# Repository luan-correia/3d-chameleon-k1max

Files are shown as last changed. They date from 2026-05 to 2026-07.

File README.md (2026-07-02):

# 3D Camaleao - 3D Chameleon modificado

Projeto de controle para um sistema tipo 3D Chameleon com:

- Raspberry Pi Pico controlando motores, sensores e comunicacao com a K1/Klipper
- ESP32 com display ST7789 atualizado, encoder e menu de configuracao
- 2 drivers TMC2209 em modo standalone
- sensores de filamento no hub, hotend, buffer e entradas T0 a T3
- arquivos Klipper e modelos STL do conjunto mecanico

Este repositorio esta organizado para documentar o hardware, os firmwares e os arquivos auxiliares usados no projeto.

## Instalacao automatica no Klipper

O instalador configura o daemon serial, as macros e o painel dedicado **Camaleao** no Mainsail. Ele detecta automaticamente Creality K1/Buildroot e instalacoes Linux comuns do Klipper.

```bash
git clone https://github.com/luan-correia/3d-chameleon-k1max.git
cd 3d-chameleon-k1max
sudo ./installer/install.sh
```

Depois da instalacao, reinicie o Klipper e atualize o navegador com `Ctrl+F5`. O instalador sempre cria backup antes de alterar arquivos.

Comandos de manutencao:

```bash
sudo ./installer/update.sh
sudo ./installer/diagnose.sh
sudo ./installer/uninstall.sh
```

Consulte [docs/instalador.md](docs/instalador.md) para requisitos, variaveis e recuperacao.

## Atualizacao do display

A versao atual substitui o display simples antigo por um painel com **ESP32 + ST7789 320x240**.

Antes, o controle visual ficava mais limitado. Agora o ESP32 faz a interface completa e conversa com o Pico por I2C. O Pico continua sendo responsavel pela logica principal dos motores e sensores.

O painel novo no ESP32 inclui:

- tela inicial com status das ferramentas T0 a T3
- status de hotend, buffer, impressao e comunicacao com o Pico
- menu por encoder
- load, unload, home, start e stop pelo display
- menu de configuracao
- calibracao e reset da calibracao
- ajuste de velocidade em porcentagem
- secador de filamento opcional, com controle de temperatura e umidade
- alertas visuais de filamento no hotend, filamento quebrado ou sensor com defeito
- logo `3DC CAMALEAO - VERSAO BRASIL`

Com essa mudanca, o projeto fica dividido assim:

```text
Pico  -> motores, sensores, comandos da K1/Klipper e seguranca
ESP32 -> display ST7789, encoder, menus, alertas e configuracao visual
```

## Estrutura

```text
firmware/
  esp32_display/
    platformio.ini
    src/ESP32_3D_Chameleon_ST7789_I2C_V16_GOTA_UMIDADE.ino
  pico/
    Pico_3D_Chameleon_I2C_COMPLETO.ino

docs/
  pinout.md
  funcionamento.md
  configuracao.md

camaleao e base/
  arquivos STL da base, hub e suporte

rebobinador/
  arquivos STL do rebobinador

klipper upgrade comunicao python e macros para camaleoa/
  macros Klipper e daemon Python

installer/
  instalacao, atualizacao, diagnostico e desinstalacao
```

## Estado atual do firmware

### Pico

O Pico e o controlador principal do sistema. Ele cuida de:

- motor seletor
- motor alimentador/extrusor
- sensores T0, T1, T2 e T3
- sensor unico do hub/saida
- sensor hotend
- sensores de buffer vazio e cheio
- endstop do seletor
- comandos USB serial vindos da K1/Klipper
- comunicacao I2C com o ESP32

### ESP32

O ESP32 cuida da interface:

- display ST7789 320x240
- encoder
- menu principal
- menu de configuracao
- alertas visuais
- envio de comandos para o Pico por I2C

O ESP32 nao movimenta os motores diretamente. Ele envia comandos para o Pico, e o Pico executa a acao com os sensores de seguranca.

## Aquecedor/secador opcional

O aquecedor e um recurso **opcional**. O 3D Camaleao funciona normalmente sem montar o secador; ele nao e necessario para selecionar, carregar ou descarregar filamento.

Quem quiser usar o recurso pode ligar ao ESP32:

| Funcao | Pino do ESP32 |
|---|---|
| Sensor de temperatura NTC | GPIO34 |
| Controle do aquecedor | GPIO26 |
| Controle do ventilador | GPIO14 |

O menu `SECAGEM FILAMENTO` permite definir temperatura e umidade. O firmware so aciona o aquecedor quando o NTC e identificado corretamente, desliga o aquecimento ao atingir o limite configurado e mantem o ventilador ligado durante o resfriamento ate a temperatura ficar abaixo de 30 C.

> **Atencao:** nao ligue o aquecedor diretamente ao ESP32. Use um modulo MOSFET adequado a tensao e corrente do aquecedor, fonte dimensionada, fusivel e protecao termica. Todos os GND devem estar em comum.

## Logica principal

- `LOAD`: carrega ate o sensor do hotend detectar filamento, depois anda mais 4 mm e enche o buffer.
- `UNLOAD`: descarrega ate o sensor do hub/saida indicar que o filamento saiu, usando a distancia configurada como limite de seguranca.
- A distancia de load/unload serve como protecao: se o filamento travar e o sensor nao mudar, o Pico para e informa erro.
- O buffer e mantido pela logica de reabastecimento durante impressao.
- O pre-load aciona quando um filamento entra no sensor de entrada, vai ate o sensor do hub e retrai 40 mm.

## Microsteps e distancia

O firmware atual assume:

```cpp
MICROSTEPS = 16
STEPS_PER_REV = 200
STEPS_PER_MM = 428.0
```

Os drivers TMC2209 estao em modo standalone. Por isso, o microstep real depende dos DIP switches/jumpers da placa do driver.

No teste atual:

- seletor funcionou com `1 2 3 ON`
- extrusor funcionou melhor com `1 ON`, `2 OFF`, `3 ON`

Se mudar a configuracao de microstep, pode ser necessario recalibrar ou ajustar `STEPS_PER_MM`.

## Como compilar o ESP32

O firmware do ESP32 usa PlatformIO.

```powershell
cd firmware\esp32_display
pio run
pio run -t upload
```

No projeto original, o upload estava usando `COM3`.

O arquivo principal do display atualizado fica em:

```text
firmware/esp32_display/src/ESP32_3D_Chameleon_ST7789_I2C_V16_GOTA_UMIDADE.ino
```

## Como gravar o Pico

Abra o arquivo do Pico na Arduino IDE ou ambiente equivalente com suporte ao Raspberry Pi Pico:

```text
firmware/pico/Pico_3D_Chameleon_I2C_COMPLETO.ino
```

Grave no Raspberry Pi Pico conectado por USB.

## Lista de materiais

| Quantidade | Item |
|---|---|
| 9 | Micro switch KW10-B |
| 1 | Raspberry Pi Pico |
| 1 | ESP32 |
| 1 | Encoder |
| 1 | Fonte 12 V ou 24 V 5 A |
| 1 | Step-down para 5 V 3 A |
| 2 | Suporte para driver |
| 2 | Driver TMC2209 ou A4988 |
| 1 | Display ST7789 240x320 |
| 4 | Parafuso M3 cabeca chata 10 mm |
| 8 | Parafuso M3 cabeca chata 15 mm com porcas |
| 4 | Parafuso M3 cabeca cilindrica 35 mm |
| 20 | Parafuso M3 cabeca cilindrica 6 mm |
| 8 | Parafuso M3 cabeca cilindrica 12 mm |
| 4 | Conector PTFE |
| 6 | Esfera de 4 mm |
| 2 m | Tubo PTFE 4 mm x 2.5 mm |
| 1 | Caixa acrilica 39 x 29 x 25 cm |
| 1 | Tomada interruptor AS-03 tripolar macho com chave gangorra |
| 1 | Porta USB tipo C |
| 4 | Molas: 8 mm de comprimento, 4 mm externo, arame de 1 mm ou 0.7 mm |
| 50 | Bucha de inserto metalico M3 x 4 mm |

Para o secador opcional, acrescente um sensor NTC, um aquecedor, um ventilador e um modulo MOSFET compativel com a carga utilizada.

## Observacoes importantes

- Todos os GND precisam estar em comum: Pico, ESP32, drivers e fonte dos motores.
- Os sinais do Pico sao 3.3 V.
- Nao conecte ou desconecte motor com o driver energizado.
- Ajuste a corrente dos TMC2209 antes de testar com filamento.
- Se o motor so vibrar, confira pares das bobinas, corrente do driver e DIP switches.

## Creditos e agradecimentos

Este projeto e uma adaptacao/modificacao feita para uso na Creality K1 Max, baseada na ideia do 3D Chameleon.

Agradecimentos aos projetos e comunidades que ajudaram como referencia:

- 3D Chameleon original: https://www.3dchameleon.com/
- Filamentalist Rewinder / ERCF: https://github.com/SkiBikePrint/Filamentalist
- ERCF v2: https://github.com/Carrot-collective/ERCF_v2

## Apoie o projeto

Se este projeto te ajudou e voce quiser apoiar para ele crescer, qualquer contribuicao ajuda nos testes, pecas, placas e melhorias.

PIX:

```text
47996781505
```

PayPal:

```text
luan.lec94@gmail.com
```

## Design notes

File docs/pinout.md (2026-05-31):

# Pinout

## Pico

### Sensores de entrada

```text
T0 entrada : GPIO 0
T1 entrada : GPIO 1
T2 entrada : GPIO 2
T3 entrada : GPIO 3
```

### I2C para ESP32

```text
SDA : GPIO 4
SCL : GPIO 5
Endereco I2C: 0x12
```

### Sensores principais

```text
Endstop seletor : GPIO 8
Sensor hotend   : GPIO 9
Buffer vazio    : GPIO 10
Buffer cheio    : GPIO 11
Sensor hub      : GPIO 12
```

### Motor seletor

```text
STEP : GPIO 16
DIR  : GPIO 17
EN   : GPIO 18
```

### Motor alimentador/extrusor

```text
STEP : GPIO 19
DIR  : GPIO 20
EN   : GPIO 21
```

## ESP32

### Display ST7789

```text
TFT_CS   : GPIO 15
TFT_DC   : GPIO 2
TFT_RST  : GPIO 4
TFT_MOSI : GPIO 23
TFT_SCLK : GPIO 18
```

### I2C para Pico

```text
SDA : GPIO 21
SCL : GPIO 22
```

### Encoder

```text
CLK : GPIO 32
DT  : GPIO 33
SW  : GPIO 25
```

### DHT22

```text
DATA : GPIO 27
```

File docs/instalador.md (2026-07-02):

# Instalador do painel Camaleao

O instalador adiciona uma placa exclusiva do 3D Camaleao ao dashboard do Mainsail e instala a comunicacao Python com o Pico.

## Sistemas suportados

- Creality K1, K1 Max e variantes com root, Moonraker e Mainsail
- Raspberry Pi e outros computadores Linux com Klipper, Moonraker, Mainsail, nginx e systemd

## Requisitos

- Pico gravado com o firmware deste repositorio
- Pico conectado por USB ao computador que executa o Klipper
- Python 3
- `unzip`
- acesso root ou `sudo`
- `gcode_shell_command.py` para usar as macros Klipper

O painel Mainsail funciona diretamente com o daemon. Caso `gcode_shell_command.py` nao esteja instalado, o diagnostico avisa e o painel ainda pode ser usado manualmente.

## Instalacao

```bash
git clone https://github.com/luan-correia/3d-chameleon-k1max.git
cd 3d-chameleon-k1max
sudo ./installer/install.sh
```

O processo:

1. Detecta K1/Buildroot ou Linux comum.
2. Localiza Mainsail, nginx e `printer.cfg`.
3. Detecta a porta do Pico.
4. Cria backup com data e hora.
5. Instala daemon, cliente e macros.
6. Instala o Mainsail personalizado em uma pasta separada.
7. Valida o nginx antes de ativar a configuracao.
8. Testa `/health` e o comando `STATUS` do Pico.

## Caminhos na K1

- Configuracao: `/usr/data/printer_data/config`
- Daemon: `/usr/data/printer_data/config/chameleon`
- Painel: `/usr/data/mainsail-chameleon`
- Estado: `/usr/data/chameleon_installer/state.env`
- Backups: `/usr/data/chameleon_backups/`

## Caminhos no Linux comum

- Daemon: `/opt/chameleon`
- Painel: `/opt/mainsail-chameleon`
- Servico: `chameleon-daemon.service`
- Estado: `/var/lib/chameleon-installer/state.env`
- Backups: `/var/backups/chameleon/`

## Configuracao manual de caminhos

Se a deteccao automatica nao encontrar algum componente, informe antes do comando:

```bash
sudo CHAMELEON_SERIAL_PORT=/dev/ttyACM0 \
  CHAMELEON_CONFIG_DIR=/home/pi/printer_data/config \
  CHAMELEON_MAINSAIL_DIR=/home/pi/mainsail \
  CHAMELEON_NGINX_CONF=/etc/nginx/sites-enabled/mainsail \
  ./installer/install.sh
```

## Diagnostico

```bash
sudo ./installer/diagnose.sh
```

Ele mostra porta serial, respostas do daemon, `STATUS` do Pico, processos e caminhos instalados.

## Atualizacao

```bash
sudo ./installer/update.sh
```

O atualizador busca o repositorio e executa novamente a instalacao, criando outro backup.

## Desinstalacao

```bash
sudo ./installer/uninstall.sh
```

O desinstalador restaura o nginx salvo, remove painel, daemon e include das macros. Os backups permanecem guardados.

## Codigo-fonte do painel

O painel foi criado sobre o Mainsail `v2.17.0`. O patch utilizado para gerar o pacote esta em `installer/mainsail-src/mainsail-v2.17.0-chameleon.patch`.

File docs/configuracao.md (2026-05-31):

# Configuracao

## Menu do ESP32

O menu do ESP32 permite:

- selecionar ferramentas T0 a T3
- executar load e unload
- fazer home
- iniciar/parar impressao
- calibrar distancia
- ajustar velocidade
- ajustar rampa
- resetar configuracao de calibracao

## Velocidades

O display mostra velocidades em porcentagem.

```text
100% = 70 mm/s
```

As velocidades principais sao:

- `VEL LOAD/UN`: velocidade rapida de load/unload
- `VEL RAMPA`: velocidade da parte final da rampa
- `RAMPA MM`: quantidade de milimetros antes do fim onde a rampa comeca

## Calibracao

A calibracao mede a distancia ate o sensor do hotend. O valor salvo e usado como base para o limite de seguranca dos movimentos.

Exemplo:

```text
calibracao = 560 mm
distancia configurada = 700 mm
```

Nesse caso, o `LOAD` continua parando no sensor do hotend. Os 700 mm sao apenas limite para detectar erro se o filamento travar.

## Reset de calibracao

O menu possui uma opcao para resetar a configuracao de calibracao. Isso invalida a configuracao salva e volta aos valores padrao.

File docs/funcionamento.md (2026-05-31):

# Funcionamento

## LOAD

O comando `LOAD` faz:

1. Verifica se o filamento ja esta no hotend.
2. Se nao estiver, gira o motor alimentador no sentido de load.
3. Para quando o sensor do hotend detectar filamento.
4. Anda mais 4 mm para encostar o filamento.
5. Enche o buffer.

A distancia configurada e usada como limite de seguranca. Se o sensor do hotend nao acionar dentro do limite, o Pico para e informa erro.

## UNLOAD

O comando `UNLOAD` faz:

1. Desativa o modo buffer drain, se estiver ativo.
2. Gira o motor alimentador no sentido de unload.
3. Para quando o sensor do hub/saida indicar que o filamento saiu.
4. Retrai mais 40 mm para o filamento nao sair do Camaleao.

A distancia configurada tambem e limite de seguranca. Se o sensor nao mudar, o Pico para e informa erro.

## PRE-LOAD

O pre-load e acionado quando um sensor de entrada muda de sem filamento para com filamento.

Fluxo:

1. Confere se o hub esta livre.
2. Se o hub ja tiver filamento, ignora para evitar colisao.
3. Move o seletor para a ferramenta detectada.
4. Empurra ate o sensor do hub detectar filamento.
5. Retrai 40 mm.

## Buffer

Durante a impressao, o Pico monitora os sensores de buffer. Quando o buffer fica vazio e o hotend ainda tem filamento, ele reabastece ate o sensor de buffer cheio.

## Alertas no ESP32

O display mostra alertas quando:

- o hotend detecta filamento e o hub nao detecta, indicando possivel filamento quebrado ou sensor com defeito
- hub e hotend detectam filamento, indicando que o filamento ja esta no hotend

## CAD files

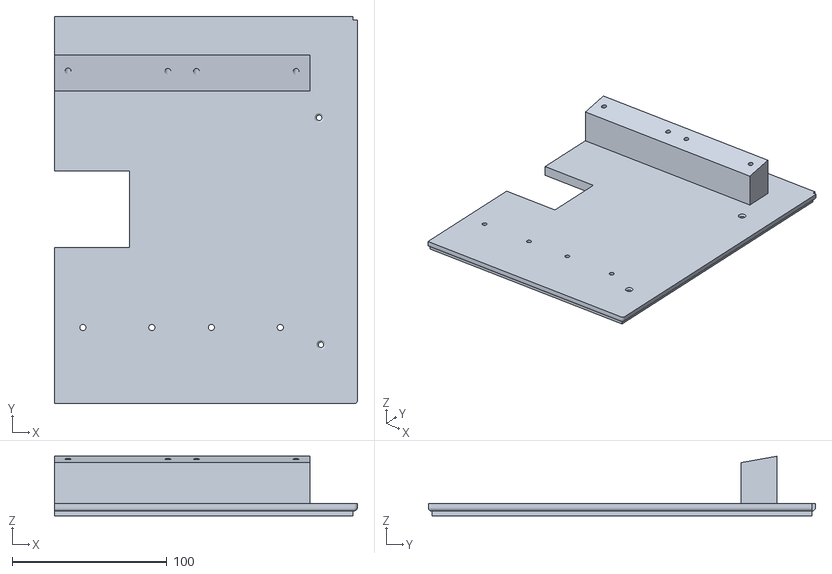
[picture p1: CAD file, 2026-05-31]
camaleao e base/tampa base 2 tampa base para nema 17 42.stl
195.7 x 250.2 x 38.4

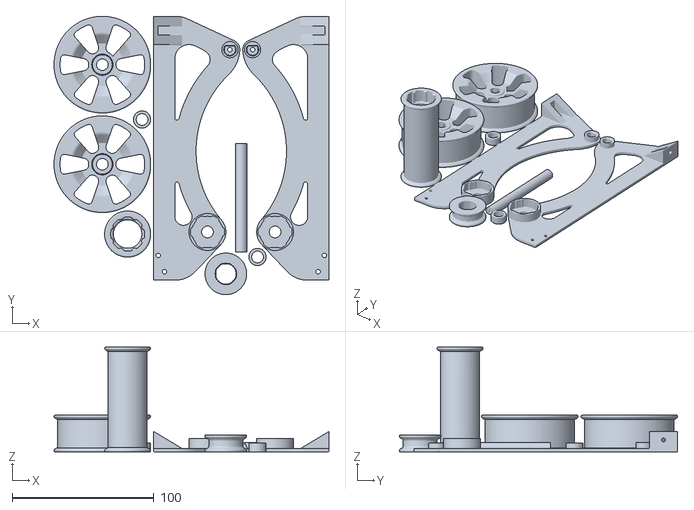
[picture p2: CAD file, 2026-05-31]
rebobinador/filamentalist.stl
193.8 x 196.2 x 74.0

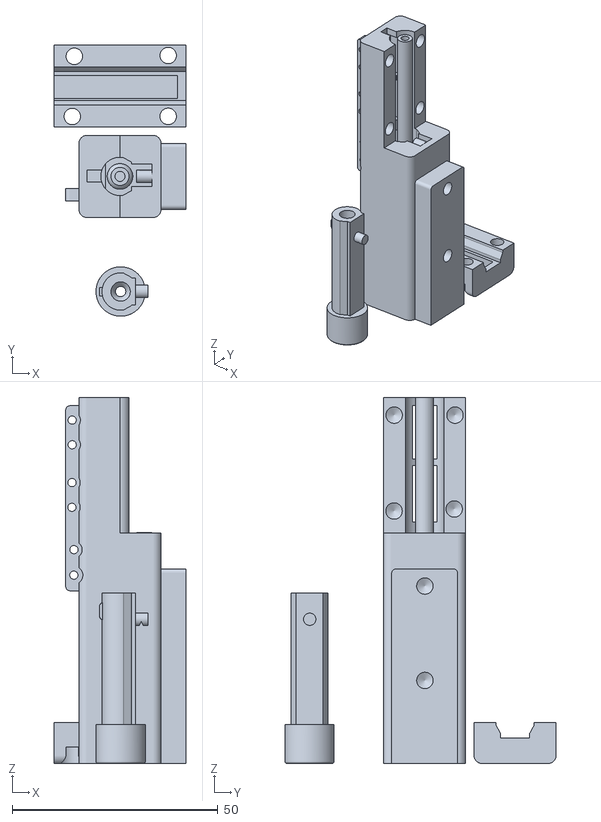
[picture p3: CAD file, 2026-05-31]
camaleao e base/hub buffe v2.stl
32.0 x 66.0 x 89.0

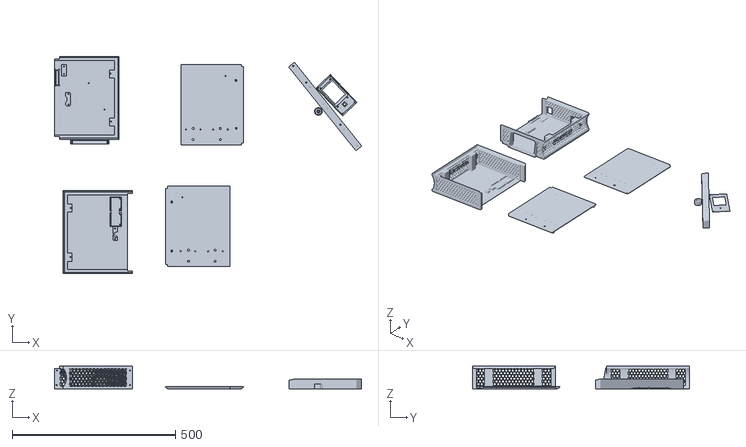
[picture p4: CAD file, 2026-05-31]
camaleao e base/base para camaleao com display.stl
939.0 x 665.1 x 70.0

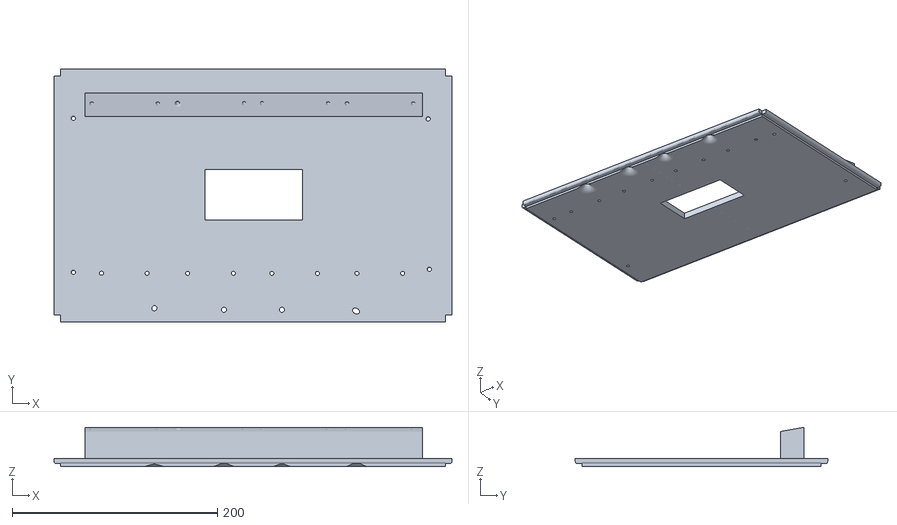
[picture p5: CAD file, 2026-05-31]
camaleao e base/tampa base para nema 17 42.stl
388.0 x 246.2 x 38.4

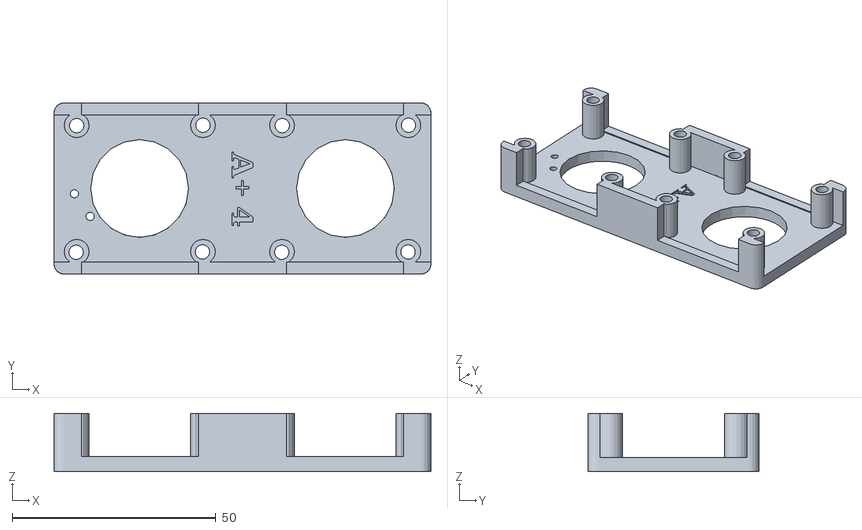
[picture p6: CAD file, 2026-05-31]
camaleao e base/camaelao 4.0 A+ com sensor home.stl
92.5 x 42.0 x 14.2

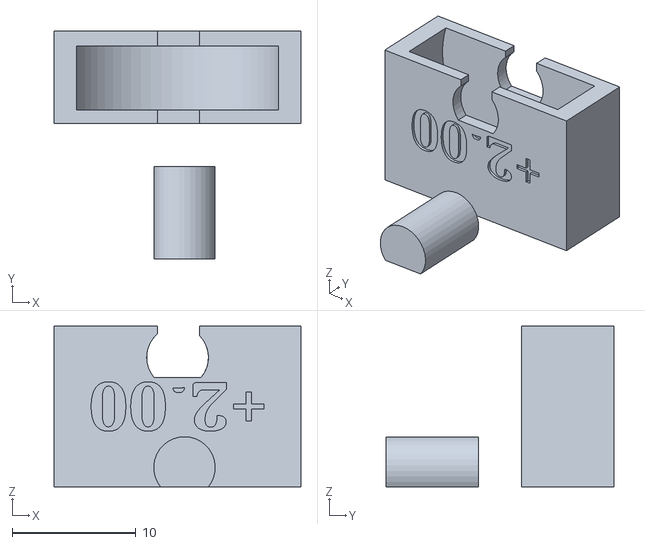
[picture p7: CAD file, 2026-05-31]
camaleao e base/suporte do rolamento de tensao do filamento.stl
20.0 x 18.5 x 13.0

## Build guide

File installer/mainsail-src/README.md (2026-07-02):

# Fonte do painel Mainsail

O arquivo `mainsail-v2.17.0-chameleon.patch` contem as mudancas aplicadas ao Mainsail oficial `v2.17.0`.

Para recompilar:

```bash
git clone --branch v2.17.0 https://github.com/mainsail-crew/mainsail.git
cd mainsail
git apply ../mainsail-v2.17.0-chameleon.patch
npm install
npm run build
```

O conteudo gerado em `dist/` deve ser compactado na raiz do ZIP e colocado em `installer/assets/mainsail-chameleon.zip`.

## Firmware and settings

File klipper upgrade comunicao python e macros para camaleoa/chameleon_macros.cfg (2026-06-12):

########################################################################################################################
# chameleon_macros.cfg — 3D Chameleon K1 Max
# Comunicação via USB Serial → Pico usando gcode_shell_command
#
# Setup:
#   1. Pico conectado via USB na K1
#   2. chameleon_bridge.py em /usr/data/chameleon_bridge.py
#   3. pip3 install pyserial
#   4. gcode_shell_command.py em /usr/share/klipper/klippy/extras/
#   5. Verificar porta: ls /dev/ttyACM* /dev/ttyUSB*
#   6. Ajustar ARDUINO_PORT no chameleon_bridge.py se necessário
#
# No printer.cfg adicionar:
#   [include chameleon_macros.cfg]
#
# Switch do hotend conectado direto no Pico GPIO9
# Não precisa de filament_switch_sensor no printer.cfg
#
# Start Gcode Creality Print:
#   CHAMELEON_PRINT_START TOOL=[initial_no_support_extruder]
#
# End Gcode:
#   CHAMELEON_PRINT_END
########################################################################################################################


# ══════════════════════════════════════════════════════════════════════════════
# SHELL COMMAND
# ══════════════════════════════════════════════════════════════════════════════

[gcode_shell_command chameleon_cmd]
command: python3 /usr/data/printer_data/config/chameleon/chameleon_client.py
timeout: 120
verbose: True

[gcode_shell_command chameleon_daemon_start]
command: /bin/sh /usr/data/printer_data/config/chameleon/chameleon-daemon.init start
timeout: 10
verbose: False

[delayed_gcode CHAMELEON_DAEMON_AUTOSTART]
initial_duration: 15
gcode:
    RUN_SHELL_COMMAND CMD=chameleon_daemon_start


# ══════════════════════════════════════════════════════════════════════════════
# VARIÁVEIS GLOBAIS
# ══════════════════════════════════════════════════════════════════════════════

[gcode_macro _CHAMELEON_VARS]
variable_tool: 0
variable_enabled: 1
variable_runout_paused: 0
variable_waiting_initial_tool: 0
gcode:
    # macro de variáveis — não executa nada


# ══════════════════════════════════════════════════════════════════════════════
# FIL_CUT — ativa buffer drain, Z hop, retrai, corta e vai para posição de purga
#
# Fluxo:
#   1. BUFFER_DRAIN → Pico esvazia buffer se cheio, ativa modo drain em background
#                     responde imediatamente, macro continua
#   2. Z hop +5mm relativo à peça atual
#   3. Move para cortador, retrai 40mm + corte duplo + retrai 70mm
#      (retração enche buffer → Pico esvazia automaticamente)
#   4. Move para posição de purga X304 Y250 Z0.2 e aguarda
#      RESTORE feito somente após Purga
# ══════════════════════════════════════════════════════════════════════════════

[gcode_macro CHAMELEON_ENABLE]
description: Ativa o MMU 3D Chameleon
gcode:
    SET_GCODE_VARIABLE MACRO=_CHAMELEON_VARS VARIABLE=enabled VALUE=1
    RESPOND MSG="Chameleon: MMU ativado."


[gcode_macro CHAMELEON_DISABLE]
description: Desativa o MMU para imprimir com filamento externo
gcode:
    SET_GCODE_VARIABLE MACRO=_CHAMELEON_VARS VARIABLE=enabled VALUE=0
    RESPOND MSG="Chameleon: MMU desativado. Comandos de troca serao ignorados."


[gcode_macro Fil_Cut]
description: Ativa buffer drain, Z hop, retrai, corta e vai para posição de purga
gcode:
    SAVE_GCODE_STATE NAME=troca_state
    {% set z_hop = 5.0 %}
    {% set max_z = printer.toolhead.axis_maximum.z %}
    {% set cur_z = printer.toolhead.position.z %}
    {% set safe_z = [cur_z + z_hop, max_z] | min %}

    # 1. Pico entra em modo BUFFER_DRAIN — responde imediatamente
    RESPOND MSG="🐍 Fil_Cut: ativando buffer drain..."
    RUN_SHELL_COMMAND CMD=chameleon_cmd PARAMS="BUFFER_DRAIN"

    # 2. Z hop seguro antes de mover
    G90
    G0 Z{safe_z} F3000

    # 3. Move para cortador
    RESPOND MSG="🐍 Fil_Cut: movendo para cortador..."
    G90
    M83

    G0 X34 Y280 F15000
    G1 E-38 F800              # Retrai 40mm rapido

    G0 X24 Y280 F15000
    G0 Y305 F1000

    # 4. Corte duplo
    RESPOND MSG="🐍 Fil_Cut: cortando..."
    G0 X7 F2000
    G0 X24 F10000
    G0 X7 F2000
    G0 X24 Y280 F10000

    G1 E-50 F1500              # Retrai 50mm rapido apos corte

    # 5. Move para posição de purga e aguarda novo filamento
    RESPOND MSG="Fil_Cut: corte concluido, chamando unload..."


# ══════════════════════════════════════════════════════════════════════════════
# PURGA — bico já está na posição X304 Y250 Z0.2 vindo do Fil_Cut
# ══════════════════════════════════════════════════════════════════════════════

[gcode_macro FIL_CUT_END]
description: Corte final - retrai, corta e faz unload sem ir para purga
gcode:
    {% set vars = printer["gcode_macro _CHAMELEON_VARS"] %}
    {% set enabled = vars.enabled|int %}
    {% set current_tool = vars.tool|int %}

    {% if not enabled %}
        RESPOND MSG="Chameleon: MMU desativado, FIL_CUT_END ignorado."
    {% else %}
        {% set z_hop = 5.0 %}
        {% set max_z = printer.toolhead.axis_maximum.z %}
        {% set cur_z = printer.toolhead.position.z %}
        {% set safe_z = [cur_z + z_hop, max_z] | min %}

        RESPOND MSG="Chameleon End: buffer drain..."
        RUN_SHELL_COMMAND CMD=chameleon_cmd PARAMS="BUFFER_DRAIN"

        G90
        G0 Z{safe_z} F3000

        RESPOND MSG="Chameleon End: movendo para cortador..."
        M83
        G0 X34 Y280 F15000
        G1 E-30 F800
        G0 X24 Y280 F15000
        G0 Y305 F1000

        RESPOND MSG="Chameleon End: cortando..."
        G0 X5 F2000
        G0 X24 F10000
        G0 X5 F2000
        G0 X24 Y280 F10000
        G4 P1500
        G1 E-50 F1500
        
        M400 
        
        G4 P500  
        
   

        RESPOND MSG="Chameleon End: descarregando T{current_tool}..."
        RUN_SHELL_COMMAND CMD=chameleon_cmd PARAMS="T{current_tool}"
        RUN_SHELL_COMMAND CMD=chameleon_cmd PARAMS="UNLOAD"
    {% endif %}

[gcode_macro Purga]
gcode:
    {% set current_temp = printer.extruder.target %}
    G90
    M83

    RESPOND MSG="Purga: formando torre na borda..."
    G0 X300 Y250 F15000
    G0 Z0.20 F2000


    G1 E70 F350
    G0 Z2 F1000 
    
    M106 S255
    
    G1 E10 F250
    G0 Z3 F1000
    G1 E10 F250
    G0 Z4 F1000
    G1 E10 F250
    G0 Z5 F1000
    G1 E10 F250
    G0 Z6 F1000
    G1 E-1 F300

    G4 P3000

    RESPOND MSG="Purga: empurrando descarte para fora da mesa..."
    G0 Z15  F1000
    G0 X280  F16000
    G0 Z2 F1000
    G0 X304 F6000
  

    G0 Z3 F3000
    M106 S0

    RESPOND MSG="Purga: limpando bico no silicone..."
    G0 X301 Y280 F15000
    G0 Y250 F15000
    G0 Y290 F15000
    G0 Y250 F15000
    G0 Y290 F15000
    G0 Y250 F15000

    RESPOND MSG="Purga: concluida."
    M104 S{current_temp}
    RESTORE_GCODE_STATE NAME=troca_state MOVE=0


[gcode_macro Purga_Inicial]
gcode:
    {% set current_temp = printer.extruder.target %}
    G90
    M83

    RESPOND MSG="Purga inicial: formando torre maior na borda..."
    G0 X300 Y250 F15000
    G0 Z0.20 F2000


    G1 E70 F350
    G0 Z2 F1000

    M106 S255

    G1 E20 F250
    G0 Z3 F1000
    G1 E20 F250
    G0 Z4 F1000
    G1 E20 F250
    G0 Z5 F1000
    G1 E10 F300
    G0 Z6 F1000
    G1 E10 F250
    G0 Z7 F1000
    G1 E10 F1000
    G0 Z9 F1000
    G1 E10 F1000
    G0 Z8 F1000
    G1 E10 F1000
    G0 Z10 F1000
    G1 E-0.2 F300

    G4 P3000

    RESPOND MSG="Purga inicial: empurrando descarte para fora da mesa..."
    G0 Z15  F1000
    G0 X280  F16000
    G0 Z2 F1000
    G0 X304 F6000


    G0 Z3 F3000
    M106 S0

    RESPOND MSG="Purga inicial: limpando bico no silicone..."
    G0 X301 Y280 F15000
    G0 Y250 F15000
    G0 Y290 F15000
    G0 Y250 F15000
    G0 Y290 F15000
    G0 Y250 F15000

    RESPOND MSG="Purga inicial: concluida."
    M104 S{current_temp}
    RESTORE_GCODE_STATE NAME=troca_state MOVE=0




# ══════════════════════════════════════════════════════════════════════════════
# LOAD_ATE_SENSOR — Pico empurra até GPIO9 acionar
# Se filamento já presente retorna imediatamente
# Após Load OK o buffer ativa automaticamente no Pico
# ══════════════════════════════════════════════════════════════════════════════

[gcode_macro Load_Ate_Sensor]
description: LOAD contínuo — para quando sensor hotend GPIO9 acionar
gcode:
    RESPOND MSG="🐍 Load: empurrando até sensor..."
    RUN_SHELL_COMMAND CMD=chameleon_cmd PARAMS="LOAD"
    RESPOND MSG="🐍 Load: filamento chegou ao sensor!"


# ══════════════════════════════════════════════════════════════════════════════
# SEQUÊNCIA DE TROCA COMPLETA
#
# Fluxo:
#   1. Fil_Cut         → BUFFER_DRAIN + Z hop + retrai + corta + vai para purga
#   2. T{atual}+UNLOAD → Pico sai do drain + descarrega até sensor saída
#   3. T{novo}         → seletor move para novo gate
#   4. Load_Ate_Sensor → Pico empurra até GPIO9 acionar → buffer ativa
#   5. Purga           → purga + limpa + volta para peça
# ══════════════════════════════════════════════════════════════════════════════
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

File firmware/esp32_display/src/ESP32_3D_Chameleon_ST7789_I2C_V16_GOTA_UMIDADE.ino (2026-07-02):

/* ════════════════════════════════════════════════════════════════════════
   3D CHAMELEON MK4
   ESP32 + ST7789 320x240
   LAYOUT CLEAN V14 — I2C Pico + ATIVO por LOAD + Menos Pisca
════════════════════════════════════════════════════════════════════════ */

#include <Adafruit_GFX.h>
#include <Adafruit_ST7789.h>
#include <SPI.h>
#include <Wire.h>
#include <DHT.h>
#include <Preferences.h>

// ═══════════════════════════════════════
// DISPLAY (VSPI — pinos padrao)
// ═══════════════════════════════════════

#define TFT_CS    15
#define TFT_DC     2
#define TFT_RST    4
#define TFT_MOSI  23
#define TFT_SCLK  18

Adafruit_ST7789 tft = Adafruit_ST7789(TFT_CS, TFT_DC, TFT_RST);

// ═══════════════════════════════════════
// I2C PICO (ESP32 mestre / Pico escravo)
//
// Ligacao ESP32 <-> Pico:
//   ESP GPIO21 (SDA) -> Pico GPIO4 (SDA)
//   ESP GPIO22 (SCL) -> Pico GPIO5 (SCL)
//   GND              -> GND
//
// Use pull-up de 4.7k em SDA e SCL para 3.3V.
// ═══════════════════════════════════════

#define PICO_I2C_SDA   21
#define PICO_I2C_SCL   22
#define PICO_I2C_ADDR  0x12

#define I2C_CMD_SIZE   4
#define I2C_STA_SIZE   16
#define I2C_SOF_CMD    0xAA
#define I2C_SOF_STA    0xBB
#define STEPS_PER_MM_F 428.0f
#define CONFIG_SPEED_MAX_MMS_F 70.0f

// Comandos
#define CMD_T0          0x01
#define CMD_T1          0x02
#define CMD_T2          0x03
#define CMD_T3          0x04
#define CMD_LOAD        0x05
#define CMD_UNLOAD      0x06
#define CMD_HOME        0x07
#define CMD_START_PRINT 0x08
#define CMD_STOP_PRINT  0x09
#define CMD_STATUS      0x0A
#define CMD_CALIBRAR    0x70
#define CMD_SPD_FAST_UP  0x80
#define CMD_SPD_FAST_DN  0x81
#define CMD_SPD_RAMP_UP  0x82
#define CMD_SPD_RAMP_DN  0x83
#define CMD_RAMP_MM_UP   0x84
#define CMD_RAMP_MM_DN   0x85
#define CMD_DIST_UP      0x86
#define CMD_DIST_DN      0x87
#define CMD_RESET_CONFIG 0x88

// Status do Pico
#define STA_IDLE     0x00
#define STA_BUSY     0x01
#define STA_PRINTING 0x02
#define STA_ERROR    0x03

// ═══════════════════════════════════════
// DHT22
// ═══════════════════════════════════════

#define DHT_PIN  27
#define DHT_TYPE DHT22
DHT dht(DHT_PIN, DHT_TYPE);

// Secagem de filamento (controle local no ESP32)
#define NTC_PIN       34
#define HEATER_PIN    26
#define DRYER_FAN_PIN 14

const float NTC_FIXED_OHMS = 100000.0f;
const float NTC_NOMINAL_OHMS = 100000.0f;
const float NTC_NOMINAL_C = 25.0f;
const float NTC_BETA = 3950.0f;
const float DRYER_COOLDOWN_C = 30.0f;
const float DRYER_HYSTERESIS_C = 1.0f;

// ═══════════════════════════════════════
// PREFERENCES
// ═══════════════════════════════════════

Preferences prefs;

// ═══════════════════════════════════════
// ENCODER
// ═══════════════════════════════════════

#define ENC_CLK 32
#define ENC_DT  33
#define ENC_SW  25

volatile int      encDelta         = 0;
volatile bool     btnPressed       = false;
volatile uint32_t lastBtnInterrupt = 0;
const int         ENC_COUNTS_PER_STEP = 2;
int               lastCLK_val      = HIGH;

// ═══════════════════════════════════════
// CORES
// ═══════════════════════════════════════

#define C_BG     0x0841
#define C_WHITE  0xFFFF
#define C_BLACK  0x0000
#define C_GRAY   0x7BEF
#define C_DARK   0x2104
#define C_CYAN   0x07FF
#define C_RED    0xF800
#define C_BLUE   0x001F
#define C_ORANGE 0xFD20
#define C_YELLOW 0xFFE0
#define C_ACTIVE 0x05BF
#define C_GREEN  0x07E0

const int COLOR_COUNT = 11;
const char* colorNames[COLOR_COUNT] = {
  "VERMELHO","VERDE","AZUL","AMARELO","LARANJA",
  "ROXO","BRANCO","CINZA","ROSA","MARROM","PRETO"
};
const uint16_t colorValues[COLOR_COUNT] = {
  0xF800, 0x07E0, 0x001F, 0xFFE0, 0xFD20,
  0x780F, 0xFFFF, 0x7BEF, 0xF81F, 0x8200, 0x0000
};

uint16_t toolColors[4] = { 0xF800, 0x07E0, 0x001F, 0xFFE0 };

// ═══════════════════════════════════════
// ESTADO ATUAL E ANTERIOR
// ═══════════════════════════════════════

struct ChameleonState {
  int   toolAtiva    = 0;
  bool  filamento[4] = { false, false, false, false };
  bool  bufferCheio  = false;
  bool  hub          = false;
  bool  hotend       = false;
  bool  imprimindo   = false;
  bool  unloadError  = false;
  float temperatura  = 0;
  float umidade      = 0;
  bool  picoOK       = false;
};

ChameleonState state;
ChameleonState prevState;
uint8_t picoStatusCode = STA_IDLE;

// Controle local do ESP32: etiqueta ATIVO aparece somente depois de LOAD
// e some depois de UNLOAD. Nao depende apenas da tool selecionada.
bool toolLoaded[4]     = { false, false, false, false };
bool prevToolLoaded[4] = { false, false, false, false };

bool homeDrawn = false;
bool unloadErrorShown = false;
bool prevDryerActive = false;

// ═══════════════════════════════════════
// NAVEGACAO
// ═══════════════════════════════════════

enum Screen {
  SCR_HOME,
  SCR_MENU,
  SCR_TOOL_ACTION,
  SCR_COLOR_SELECT,
  SCR_CONFIG,        // submenu de configuracoes
  SCR_DRYER
};

struct DryerState {
  float temperature = NAN;
  int targetTemperature = 50;
  int targetHumidity = 20;
  bool ntcOK = false;
  bool active = false;
  bool cooling = false;
  bool heaterOn = false;
  bool fanOn = false;
};

DryerState dryer;
int dryerIdx = 0;
bool dryerEditing = false;
const int DRYER_COUNT = 4;
unsigned long lastDryerControl = 0;
unsigned long lastDryerDraw = 0;

// Estado das configuracoes recebidas do Pico
struct ConfigState {
  float distMax  = 4000.0;
  int   spdFast  = 28;
  int   spdRamp  = 1325;
  float rampMM   = 60.0;
  bool  calibrado = false;
};

ConfigState cfg;

// Qual item do submenu config esta sendo editado
int cfgIdx = 0;
bool cfgEditing = false;
int cfgFastPercentEdit = 0;
int cfgRampPercentEdit = 0;

const int CONFIG_COUNT = 7;  // Calibrar + 4 ajustes + Reset + Voltar

Screen currentScreen = SCR_HOME;

int menuIdx      = 0;
int prevMenuIdx  = -1;
int toolActionIdx = 0;
int selectedToolIdx = 0;
int colorToolIdx = 0;
int colorPickIdx = 0;

const int TOOL_ACTION_COUNT = 4;
const char* toolActionLabels[TOOL_ACTION_COUNT] = {
  "EXTRUSAO",
  "RETRAIR",
  "COR FILAMENTO",
  "< VOLTAR"
};

// ═══════════════════════════════════════
// MENU
// ═══════════════════════════════════════

const int   MENU_COUNT = 12;
const char* menuLabels[MENU_COUNT] = {
  "< VOLTAR",
  "FILAMENTO T0","FILAMENTO T1","FILAMENTO T2","FILAMENTO T3",
  "LOAD","UNLOAD","HOME",
  "START","STOP",
  "SECAGEM FILAMENTO",
  "CONFIGURACAO"
};
const uint8_t menuCmds[MENU_COUNT] = {
  0x00,
  CMD_T0, CMD_T1, CMD_T2, CMD_T3,
  CMD_LOAD, CMD_UNLOAD, CMD_HOME,
  CMD_START_PRINT, CMD_STOP_PRINT,
  0x00,
  0x00  // CONFIGURACAO — tratado localmente
};

// ═══════════════════════════════════════
// FEEDBACK
// ═══════════════════════════════════════

bool          showingFeedback = false;
unsigned long feedbackStart   = 0;

// ═══════════════════════════════════════
// TIMERS
// ═══════════════════════════════════════

unsigned long lastDHT     = 0;
unsigned long lastRefresh = 0;

// ═══════════════════════════════════════
// ISR
// ═══════════════════════════════════════

void IRAM_ATTR encoderISR() {
  int clk = digitalRead(ENC_CLK);
  int dt  = digitalRead(ENC_DT);
  if (clk != lastCLK_val) {
    encDelta += (dt != clk) ? 1 : -1;
    lastCLK_val = clk;
  }
}

void IRAM_ATTR buttonISR() {
  uint32_t now = millis();
  if (now - lastBtnInterrupt > 500) {
    btnPressed       = true;
    lastBtnInterrupt = now;
  }
}

// ═══════════════════════════════════════
// I2C PICO
// ═══════════════════════════════════════

uint8_t i2cChecksum(uint8_t* buf, int len) {
  uint8_t chk = 0;
  for (int i = 0; i < len; i++) chk ^= buf[i];
  return chk;
}

bool picoReadStatus() {
  uint8_t rxBuf[I2C_STA_SIZE] = {0};

  int n = Wire.requestFrom(PICO_I2C_ADDR, I2C_STA_SIZE);
  if (n != I2C_STA_SIZE) {
    while (Wire.available()) Wire.read();
    return false;
  }

  for (int i = 0; i < I2C_STA_SIZE; i++) {
    rxBuf[i] = Wire.read();
  }

  if (rxBuf[0] != I2C_SOF_STA) return false;
  if (i2cChecksum(rxBuf, I2C_STA_SIZE - 1) != rxBuf[I2C_STA_SIZE - 1]) return false;

  // Pico envia:
  // [0xBB][STA][T][FILS][BUF][HE][FLAGS][DIST_LH][FAST_LH][RAMP_LH][RAMP_MM_LH][CHK]
  uint8_t sta  = rxBuf[1];
  uint8_t tool = rxBuf[2];
  uint8_t fils = rxBuf[3];
  uint8_t flags = rxBuf[6];

  state.picoOK    = true;
  state.toolAtiva = (tool > 0 && tool <= 4) ? tool - 1 : 0;
  picoStatusCode  = sta;

  for (int i = 0; i < 4; i++) {
    state.filamento[i] = (fils >> i) & 0x01;
  }

  state.bufferCheio = rxBuf[4] & 0x01;
  state.hub         = rxBuf[4] & 0x02;
  state.hotend      = rxBuf[5] & 0x01;
  state.imprimindo  = (sta == STA_PRINTING) || (flags & 0x01);
  state.unloadError = flags & 0x04;

  cfg.calibrado = flags & 0x02;
  cfg.distMax   = (float)((uint16_t)rxBuf[7]  | ((uint16_t)rxBuf[8]  << 8));
  cfg.spdFast   =         (uint16_t)rxBuf[9]  | ((uint16_t)rxBuf[10] << 8);
  cfg.spdRamp   =         (uint16_t)rxBuf[11] | ((uint16_t)rxBuf[12] << 8);
  cfg.rampMM    = (float)((uint16_t)rxBuf[13] | ((uint16_t)rxBuf[14] << 8));

  return true;
}

bool picoSendOnly(uint8_t cmd, uint8_t arg = 0) {
  uint8_t txBuf[I2C_CMD_SIZE] = {0};

  txBuf[0] = I2C_SOF_CMD;
  txBuf[1] = cmd;
  txBuf[2] = arg;
  txBuf[3] = i2cChecksum(txBuf, 3);

  Wire.beginTransmission(PICO_I2C_ADDR);
  Wire.write(txBuf, I2C_CMD_SIZE);
  uint8_t err = Wire.endTransmission();

  return err == 0;
}

bool picoTransaction(uint8_t cmd, uint8_t arg = 0) {
  if (!picoSendOnly(cmd, arg)) return false;
  delay(10);
  return picoReadStatus();
}

void picoPollStatus() {
  // Primeiro tenta leitura direta; se falhar, tenta pedir STATUS.
  if (!picoReadStatus()) {
    if (!picoTransaction(CMD_STATUS)) {
      state.picoOK = false;
    }
  }
}

bool picoSendCommand(uint8_t cmd, uint8_t arg = 0) {
  bool ok = picoTransaction(cmd, arg);
  if (!ok) {
    delay(60);
    ok = picoTransaction(cmd, arg);
  }
  return ok;
}

bool picoSendCommandWait(uint8_t cmd, uint8_t arg = 0, unsigned long timeoutMs = 30000) {
  if (!picoSendOnly(cmd, arg)) return false;

  unsigned long start = millis();
  bool gotStatus = false;

  while (millis() - start < timeoutMs) {
    delay(120);
    if (picoReadStatus()) {
      gotStatus = true;
      if (picoStatusCode != STA_BUSY) return picoStatusCode != STA_ERROR;
    }
  }

  return gotStatus && picoStatusCode != STA_ERROR;
}

float speedUsToMMS(uint16_t delayUs) {
  if (delayUs == 0) return 0.0f;
  return 1000000.0f / (2.0f * (float)delayUs * STEPS_PER_MM_F);
}

void printSpeedPercent(uint16_t delayUs) {
  float mmS = speedUsToMMS(delayUs);
  int percent = (int)((mmS * 100.0f / CONFIG_SPEED_MAX_MMS_F) + 0.5f);
  if (percent < 1 && mmS > 0.0f) percent = 1;
  if (percent > 100) percent = 100;
  tft.print(percent);
  tft.print("%");
}

int speedUsToPercent(uint16_t delayUs) {
  float mmS = speedUsToMMS(delayUs);
  int percent = (int)((mmS * 100.0f / CONFIG_SPEED_MAX_MMS_F) + 0.5f);
  if (percent < 1 && mmS > 0.0f) percent = 1;
  if (percent > 100) percent = 100;
  return percent;
}

uint16_t percentToSpeedUs(int percent) {
  if (percent < 1) percent = 1;
  if (percent > 100) percent = 100;
  float mmS = CONFIG_SPEED_MAX_MMS_F * ((float)percent / 100.0f);
  float delayUs = 1000000.0f / (2.0f * mmS * STEPS_PER_MM_F);
  if (delayUs < 10.0f) delayUs = 10.0f;
  if (delayUs > 5000.0f) delayUs = 5000.0f;
  return (uint16_t)(delayUs + 0.5f);
}

void printSpeedValue(uint16_t delayUs) {
  float mmS = speedUsToMMS(delayUs);
  if (mmS >= 10.0f) tft.print((int)(mmS + 0.5f));
  else tft.print(mmS, 1);
  tft.print("mm/s");
}

// ═══════════════════════════════════════
// PREFERENCES
// ═══════════════════════════════════════

void saveColors() {
  prefs.begin("chameleon", false);
  prefs.putUShort("c0", toolColors[0]);
  prefs.putUShort("c1", toolColors[1]);
  prefs.putUShort("c2", toolColors[2]);
  prefs.putUShort("c3", toolColors[3]);
  prefs.end();
}

void loadColors() {
  prefs.begin("chameleon", true);
  toolColors[0] = prefs.getUShort("c0", 0xF800);
  toolColors[1] = prefs.getUShort("c1", 0x07E0);
  toolColors[2] = prefs.getUShort("c2", 0x001F);
  toolColors[3] = prefs.getUShort("c3", 0xFFE0);
  prefs.end();
}

// ═══════════════════════════════════════
// DHT
// ═══════════════════════════════════════

void readDHT() {
  float t = dht.readTemperature();
  float h = dht.readHumidity();
  if (!isnan(t)) state.temperatura = t;
  if (!isnan(h)) state.umidade     = h;
}

// ═══════════════════════════════════════
// COPIA ESTADO
// ═══════════════════════════════════════

void copyStateToPrev() {
  prevState = state;
  prevDryerActive = dryer.active;
  for (int i = 0; i < 4; i++) {
    prevToolLoaded[i] = toolLoaded[i];
  }
}

// ═══════════════════════════════════════
// UPDATE PARCIAL
// ═══════════════════════════════════════

void updateHomePartial() {
  for (int i = 0; i < 4; i++) {
    bool toolMudou  = (i == state.toolAtiva) != (i == prevState.toolAtiva);
    bool filMudou   = state.filamento[i] != prevState.filamento[i];
    bool loadMudou  = toolLoaded[i] != prevToolLoaded[i];

    if (toolMudou || filMudou || loadMudou) {
      drawRolo(i);
    }
  }

  // Compara inteiros para evitar pisca por variacao decimal pequena do DHT.
  if ((int)state.temperatura != (int)prevState.temperatura ||
      (int)state.umidade     != (int)prevState.umidade ||
      state.picoOK           != prevState.picoOK ||
      dryer.active           != prevDryerActive) {
    drawTempUmidade();
  }

  if (state.hotend      != prevState.hotend)      drawCardHotend();
  if (state.hub         != prevState.hub)         drawCardHub();
  if (state.bufferCheio != prevState.bufferCheio) drawCardBuffer();
  if (state.imprimindo  != prevState.imprimindo)  drawCardPrint();

  copyStateToPrev();
}

// ═══════════════════════════════════════
// SETUP
// ═══════════════════════════════════════

void setup() {
  Serial.begin(115200);

  pinMode(HEATER_PIN, OUTPUT);
  pinMode(DRYER_FAN_PIN, OUTPUT);
  digitalWrite(HEATER_PIN, LOW);
  digitalWrite(DRYER_FAN_PIN, LOW);

  // VSPI — display
  SPI.begin(TFT_SCLK, -1, TFT_MOSI, TFT_CS);
  tft.init(240, 320);
  tft.setRotation(3);
  tft.invertDisplay(false);
  tft.setSPISpeed(40000000);
  tft.fillScreen(C_BLACK);

  // I2C — Pico
  Wire.begin(PICO_I2C_SDA, PICO_I2C_SCL);
  Wire.setClock(100000);
  Wire.setTimeOut(20);   // evita travar display se o Pico demorar no I2C

  // DHT22
  dht.begin();

  // Encoder
  pinMode(ENC_CLK, INPUT_PULLUP);
  pinMode(ENC_DT,  INPUT_PULLUP);
  pinMode(ENC_SW,  INPUT_PULLUP);
  lastCLK_val = digitalRead(ENC_CLK);
  attachInterrupt(digitalPinToInterrupt(ENC_CLK), encoderISR, CHANGE);
  attachInterrupt(digitalPinToInterrupt(ENC_SW),  buttonISR,  FALLING);

  loadColors();
  prefs.begin("dryer", true);
  dryer.targetTemperature = prefs.getInt("temp", 50);
  dryer.targetHumidity = prefs.getInt("humidity", 20);
  prefs.end();
  drawSplash();
  delay(1200);
  readDHT();

  // Primeira leitura do Pico
  picoPollStatus();

  drawHomeFull();
  copyStateToPrev();
}

// ═══════════════════════════════════════
// LOOP
// ═══════════════════════════════════════

void loop() {
  handleEncoder();
  handleButton();
  handleSerial();

  if (millis() - lastDryerControl >= 250) {
    controlDryer();
    lastDryerControl = millis();
  }

  if (millis() - lastDHT > 2500) {
    readDHT();
    lastDHT = millis();
  }

  if (currentScreen == SCR_DRYER && millis() - lastDryerDraw >= 1000) {
    drawDryerStatus();
    lastDryerDraw = millis();
  }

  if (currentScreen == SCR_HOME && !showingFeedback) {

    // Poll Pico em ritmo mais calmo para reduzir piscadas no display.
    if (millis() - lastRefresh > 1000) {
      picoPollStatus();
      if (state.unloadError && !unloadErrorShown) {
        unloadErrorShown = true;
        drawLoadAlert();
        delay(3000);
        drawHomeFull();
        copyStateToPrev();
      } else if (!state.unloadError) {
        unloadErrorShown = false;
      }
      updateHomePartial();
      lastRefresh = millis();
    }

  }
}

// ═══════════════════════════════════════
// CONTROLE SERIAL
// Comandos via monitor serial 115200:
//   U    → encoder cima (menu sobe)
//   D    → encoder baixo (menu desce)
//   OK   → botão confirmar
//   HOME → volta para tela home
//   SIM  → simula dados para teste
// ═══════════════════════════════════════

String serialCmd = "";

void handleSerial() {
  while (Serial.available()) {
    char c = Serial.read();
    if (c == '\n' || c == '\r') {
      serialCmd.trim();
      serialCmd.toUpperCase();

      if (serialCmd == "U") {
        // Simula encoder para cima
        encDelta = ENC_COUNTS_PER_STEP;
        handleEncoder();

      } else if (serialCmd == "D") {
        // Simula encoder para baixo
        encDelta = -ENC_COUNTS_PER_STEP;
        handleEncoder();

      } else if (serialCmd == "OK") {
        // Simula botão
        btnPressed = true;
        handleButton();

      } else if (serialCmd == "HOME") {
        currentScreen = SCR_HOME;
        drawHomeFull();
        copyStateToPrev();
        Serial.println(">> Home");

      } else if (serialCmd == "SIM") {
        // Simula dados para teste visual
        state.filamento[0] = !state.filamento[0];
        state.filamento[1] = true;
        state.filamento[2] = false;
        state.filamento[3] = !state.filamento[3];
        state.bufferCheio  = !state.bufferCheio;
        state.hotend       = !state.hotend;
        state.imprimindo   = !state.imprimindo;
        state.temperatura  = 27.5;
        state.umidade      = 62.0;
        state.picoOK       = true;
        toolLoaded[state.toolAtiva] = state.hotend && state.bufferCheio;
        updateHomePartial();
        Serial.println(">> Dados simulados");

      } else if (serialCmd.startsWith("TOOL ")) {
        int t = serialCmd.substring(5).toInt();
        if (t >= 0 && t <= 3) {
          state.toolAtiva = t;
          updateHomePartial();
          Serial.print(">> Tool "); Serial.println(t);
        }

      } else if (serialCmd != "") {
        Serial.println("Cmds: U D OK HOME SIM TOOL 0-3");
      }

      serialCmd = "";
    } else {
      serialCmd += c;
    }
  }
}

// ═══════════════════════════════════════
// ENCODER
// ═══════════════════════════════════════

void handleEncoder() {
  int delta = 0;
  noInterrupts();
  if      (encDelta >= ENC_COUNTS_PER_STEP)  { delta =  1; encDelta = 0; }
  else if (encDelta <= -ENC_COUNTS_PER_STEP) { delta = -1; encDelta = 0; }
  interrupts();
  if (delta == 0) return;

  switch (currentScreen) {
    case SCR_MENU:
    {
      int oldIdx = menuIdx;
      menuIdx += delta;
      if (menuIdx < 0)           menuIdx = MENU_COUNT - 1;
      if (menuIdx >= MENU_COUNT) menuIdx = 0;
      drawMenuPartial(oldIdx);
      break;
    }

    case SCR_TOOL_ACTION:
      toolActionIdx += delta;
      if (toolActionIdx < 0) toolActionIdx = TOOL_ACTION_COUNT - 1;
      if (toolActionIdx >= TOOL_ACTION_COUNT) toolActionIdx = 0;
      drawToolActionMenu();
      break;

    case SCR_COLOR_SELECT:
      colorPickIdx += delta;
      if (colorPickIdx < 0)            colorPickIdx = COLOR_COUNT - 1;
      if (colorPickIdx >= COLOR_COUNT) colorPickIdx = 0;
      drawColorSelect();
      break;

    case SCR_CONFIG:
      // Configuracao agora funciona igual menu:
      // gira navega; OK entra/sai da edicao dos valores.
      if (cfgEditing && cfgIdx >= 1 && cfgIdx <= 4) {
        adjustConfig(cfgIdx, delta);
        drawConfig();
      } else {
        cfgIdx += delta;
        if (cfgIdx < 0)                cfgIdx = CONFIG_COUNT - 1;
        if (cfgIdx >= CONFIG_COUNT)    cfgIdx = 0;
        drawConfig();
      }
      break;

    case SCR_DRYER:
      if (dryerEditing && (dryerIdx == 1 || dryerIdx == 2)) {
        if (dryerIdx == 1) {
          dryer.targetTemperature += delta;
          if (dryer.targetTemperature < 30) dryer.targetTemperature = 30;
          if (dryer.targetTemperature > 80) dryer.targetTemperature = 80;
        } else {
          dryer.targetHumidity += delta;
          if (dryer.targetHumidity < 5) dryer.targetHumidity = 5;
          if (dryer.targetHumidity > 60) dryer.targetHumidity = 60;
        }
      } else {
        dryerIdx += delta;
        if (dryerIdx < 0) dryerIdx = DRYER_COUNT - 1;
        if (dryerIdx >= DRYER_COUNT) dryerIdx = 0;
      }
      drawDryer();
      break;

    default:
      break;
  }
}

// ═══════════════════════════════════════
// BOTAO
// ═══════════════════════════════════════
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

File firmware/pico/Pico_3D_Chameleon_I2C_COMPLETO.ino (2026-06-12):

/* ═══════════════════════════════════════════════════════════════════════════
   Firmware 3DChameleon Mk4 — Raspberry Pi Pico + 2x TMC2209 Standalone
   Comunicação K1 Max : USB Serial nativo — 115200 baud
   Comunicação ESP32  : I2C Slave — GPIO 4/5

   Pinout:
   ── Sensores Entrada de Filamento (NC) ──
     T0 entrada : GPIO 0  (Pino 1)
     T1 entrada : GPIO 1  (Pino 2)
     T2 entrada : GPIO 2  (Pino 4)
     T3 entrada : GPIO 3  (Pino 5)

   ── Sensor Saida Unico (NC) — compartilhado T0-T3 ──
     Saida      : GPIO 12 (Pino 16)

   ── Endstop Seletor (NC) ──
     Endstop    : GPIO 8  (Pino 11)

   ── Sensor Hotend (NC) ──
     Hotend     : GPIO 9  (Pino 12)

   ── Sensores Buffer (NC) ──
     Buffer Vazio : GPIO 10 (Pino 14)
     Buffer Cheio : GPIO 11 (Pino 15)

   ── Motor Seletor (TMC2209 standalone) ──
     STEP : GPIO 16 (Pino 21)
     DIR  : GPIO 17 (Pino 22)
     EN   : GPIO 18 (Pino 24)

   ── Motor Alimentador (TMC2209 standalone) ──
     STEP : GPIO 19 (Pino 25)
     DIR  : GPIO 20 (Pino 26)
     EN   : GPIO 21 (Pino 27)

   ── I2C Slave — ESP32 ──
     SDA : GPIO 4  (Pino 6)
     SCL : GPIO 5  (Pino 7)
     Endereço: 0x12

   Protocolo I2C:
     ESP → Pico : pacote 4 bytes [0xAA][CMD][ARG][CHK]
     Pico -> ESP : pacote 16 bytes [0xBB][ST][T][FILS][BUF][HE][FLAGS][DIST][FAST][RAMP][RAMP_MM][CHK]

   Comandos Serial USB (115200 baud) — K1 Max:
     T0-T3 HOME IDLE LOAD LOAD<mm> UNLOAD UNLOAD_RETRACAO<mm>
     BUFFER_DRAIN START_PRINT STOP_PRINT STATUS
═══════════════════════════════════════════════════════════════════════════ */

#include <EEPROM.h>
#include <Wire.h>

// ── I2C Slave — ESP32 ─────────────────────────────────
#define I2C_SDA   4
#define I2C_SCL   5
#define I2C_ADDR  0x12

#define CMD_PKT_SIZE  4
#define ST_PKT_SIZE   16

#define PKT_CMD   0xAA  // ESP → Pico
#define PKT_ST    0xBB  // Pico → ESP

#define I2C_CMD_T0          0x01
#define I2C_CMD_T1          0x02
#define I2C_CMD_T2          0x03
#define I2C_CMD_T3          0x04
#define I2C_CMD_LOAD        0x05
#define I2C_CMD_UNLOAD      0x06
#define I2C_CMD_HOME        0x07
#define I2C_CMD_START       0x08
#define I2C_CMD_STOP        0x09
#define I2C_CMD_STATUS      0x0A
#define I2C_CMD_CALIBRAR    0x70
#define I2C_CMD_SPD_FAST_UP 0x80
#define I2C_CMD_SPD_FAST_DN 0x81
#define I2C_CMD_SPD_RAMP_UP 0x82
#define I2C_CMD_SPD_RAMP_DN 0x83
#define I2C_CMD_RAMP_MM_UP  0x84
#define I2C_CMD_RAMP_MM_DN  0x85
#define I2C_CMD_DIST_UP     0x86
#define I2C_CMD_DIST_DN     0x87
#define I2C_CMD_RESET_CONFIG 0x88

#define STA_IDLE     0x00
#define STA_BUSY     0x01
#define STA_PRINTING 0x02
#define STA_ERROR    0x03
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

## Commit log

2026-03-09 Update README.md
    Foi adicionado na lista de material
2026-03-09 Add files via upload
    Arquivos para imprimir
    [+1.step, Base 3DChamaleon.step, sensor chamaleon.step]
2026-03-09 Update README.md
    Extrusora com cortador para k1
2026-03-09 Add files via upload
    hub para ptfe
    [hub 4x1.step]
2026-03-10 Update chameleon_bridge.py
    adicionado protecao quando filamento nao ser carregado,vai pausar a impressão
2026-03-10 Update chameleon_macros.cfg
    adicionado pausa se nao carregar o filamento,foi alterado posicao do restore impressao para evitar colisao apos a purga
    [chameleon_macros.cfg]
2026-03-13 adiconado um display e encoder para facilitar
2026-03-14 Update chameleon_pico_display v2.ino
    alteracao na distancia de load e unload para 4000mm ,se sua distancia for maior que 4000m do extrusor do camaleon ate hotend aumentar no codigo ino
2026-03-29 Update chameleon_macros.cfg
    adicionado um corte e retracao no end print
    [chameleon_macros.cfg]
2026-03-29 Add files via upload
    aki esta o novo hub com buffer tudo junto para diminiur espaço
    [hub buffe v2.stl]
2026-05-05 Update chameleon_macros.cfg
    fim de impressao atualizado
    [chameleon_macros.cfg]
2026-05-31 Organiza projeto 3D Camaleao
    [base para camaleao com display.stl, camaelao 4.0 A+ com sensor home.stl, chameleon_macros.cfg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]
2026-05-31 Documenta display ESP32 ST7789
2026-05-31 Remove arquivos antigos e atualiza creditos
    [+1.step, Base 3DChamaleon.step, adicionado uma bucha para parafuso home.stl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]
2026-05-31 Adiciona lista de materiais
2026-06-12 Atualiza firmwares e integracao Klipper
    [chameleon_macros.cfg]
